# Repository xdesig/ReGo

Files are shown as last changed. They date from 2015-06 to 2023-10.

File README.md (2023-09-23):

# Rego

> [!NOTE]
> Docu in Galician language

Controlador/programador de rego con varias saidas e entradas de sensado

## [Versión 0V3.][ReGo0v3]
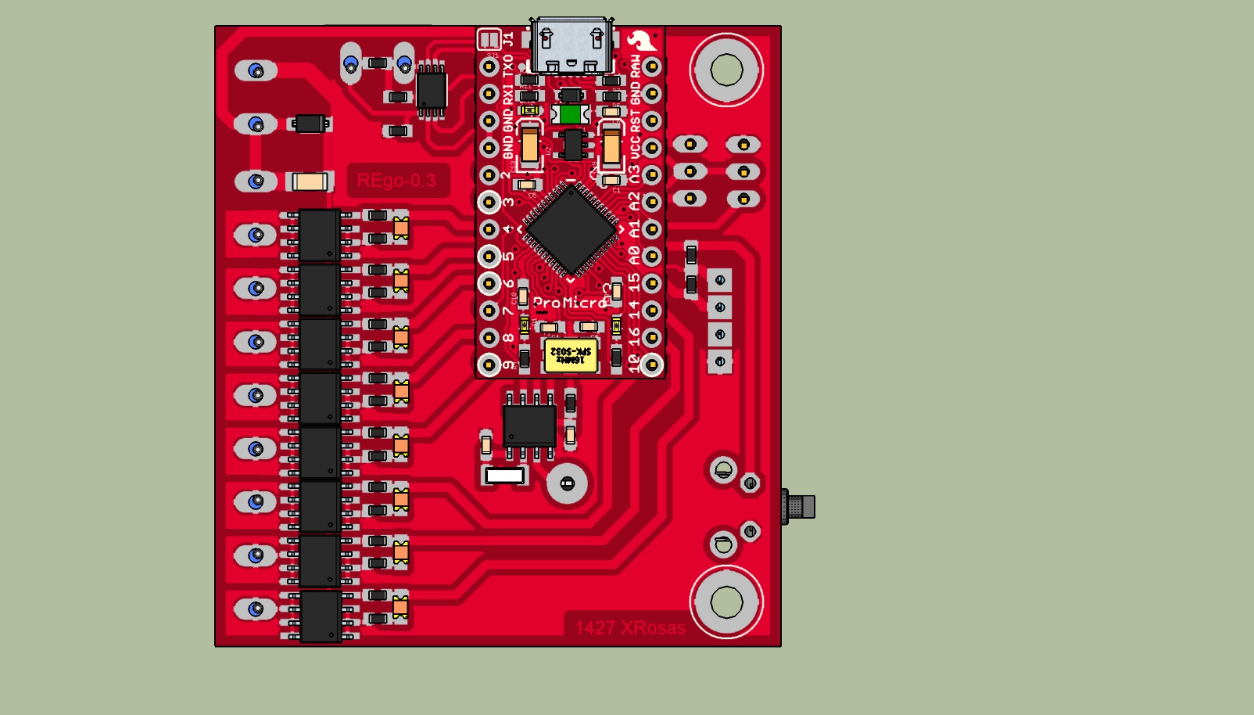
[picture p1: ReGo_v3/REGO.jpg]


Na versión 3 utilizase un Arduino ProMicro, Ten dúas entradas para sensores de humidade, un DTH11 para sensar a humidade e temperatura ambiental permite controlar oito saídas mediante Mosfets en surtidor común. Conta con un RTC PCF8523T e comunicacións USB e I2C

## [Versión 0V401.][ReGo0v4]
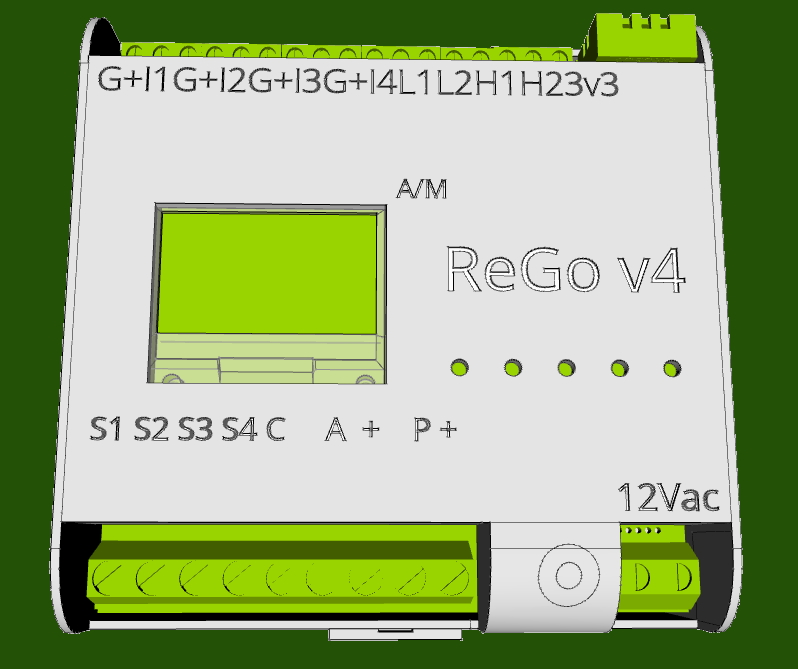
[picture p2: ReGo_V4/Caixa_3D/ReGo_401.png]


Aqui xa temos un ESP-WROOM-32, con comunicación WiFi, ten unha pantalla oled 128x64 pix, unha botoeira analóxica de cinco pulsadores, catro entradas para sensores capacitivos, dúas entradas activas a nivel alto e dúas entradas activas a nivel baixo, que poden ser usadas como finais de carreira para fiestras... ou para outos fins, conta con entrada para sensores tipo DHT11
ten un RTC PCF8523T, catro saídas a SSR (Mosfet) de 1A/30V ac ou DC adicadas xeralmente a activar as electrovalvulas ten tamén dúas saídas en surtidor común 2A/30V (por exemplo para controlar os motoes das fiestras).

* ###  Deseñado en Estrimia con agarimo.

## Author and license
* Author: [XDeSIG][TWI01]
* License: [CERN Open Hardware Licence Version 2 - Weakly Reciprocal][CERN-OHL-W]


* Certification: [OSHWA UID ES000038][OSHWA]

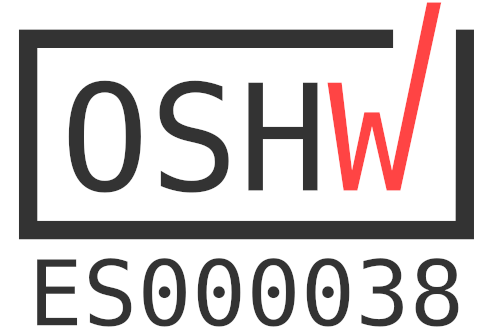
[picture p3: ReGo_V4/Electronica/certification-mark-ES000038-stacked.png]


* ### To buy boards

Developer don't produce boards to sell. Under [_provider_][provider]
directory there are instructions to order yourself.

<!-- links -->
[ReGo0v3]: https://github.com/xdesig/ReGo/tree/master/ReGo_v3
[ReGo0v4]: https://github.com/xdesig/ReGo/tree/master/ReGo_V4

[CERN-OHL-W]: https://ohwr.org/cern_ohl_w_v2.pdf
[TWI01]: https://twitter.com/xdesig
[provider]: https://www.pcbway.com/project/shareproject/Controlador_de_ReGo_V401_bd0da5d6.html
[OSHWA]: https://certification.oshwa.org/es000038.html

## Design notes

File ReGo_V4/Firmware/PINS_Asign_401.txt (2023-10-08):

/*
 * Configuracion de entadas saidas para ReGo 0.401
 * xdesig 2023
 */
// I2C 
#define SDA 
#define SCL 

//*** Entradas ***
// sensores humidade
#define IN_1 39 //SVN  	//Entrada sensor 
#define IN_2 35      	//Entrada sensor 
#define IN_3 33        	//Entrada sensor
#define IN_4 34      	//Entrada sensor

#define KEY 36 //A0     //SPV Entrada teclado 

// finais de carrera
#define IL_1 18      //Entrada Activo baixo 1
#define IL_2 19      //Entrada Activo baixo 2
#define IH_1 23      //Entrada Activo alto 1
#define IH_2 14      //Entrada Activo alto 2 

//*** Salidas ***
// DTH
#define DTHpin 17        //Entrada sensor humidade temperatura DTH

// RTC PCF8523 soldado PCF8563!
#define INT 4         //Interrupción RTC

// Electrovalvúlas
#define SAL_1 27         // Electrovalvúla  
#define SAL_2 25         // Electrovalvúla
#define SAL_3 12  //TD1  // Electrovalvúla 
#define SAL_4  0         // Electrovalvúla 

// Motores
#define ACT_1 2       	 // Pechar
#define ACT_2 15 //TD02  // Abrir

// LED Auto/Manual
#define GREEN 9       // GREEN (RED = 0 GREEN = 1) SD3
#define RED 10        // RED   (RED = 1 GREEN = 0) SD2

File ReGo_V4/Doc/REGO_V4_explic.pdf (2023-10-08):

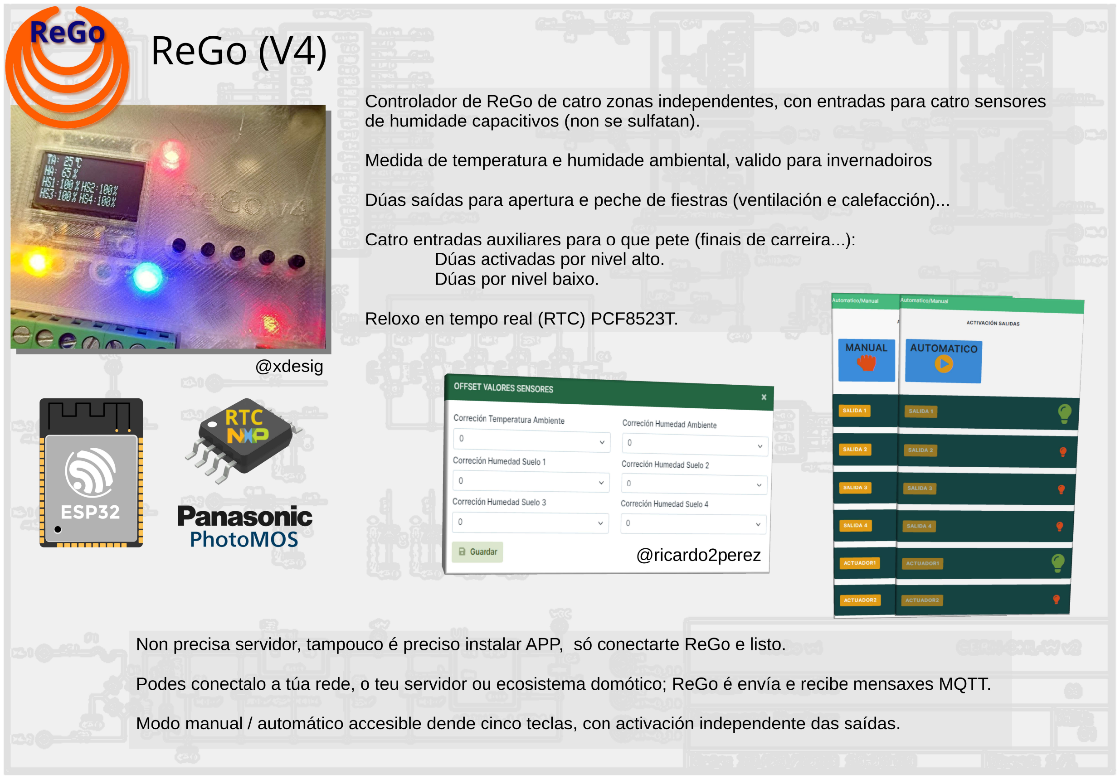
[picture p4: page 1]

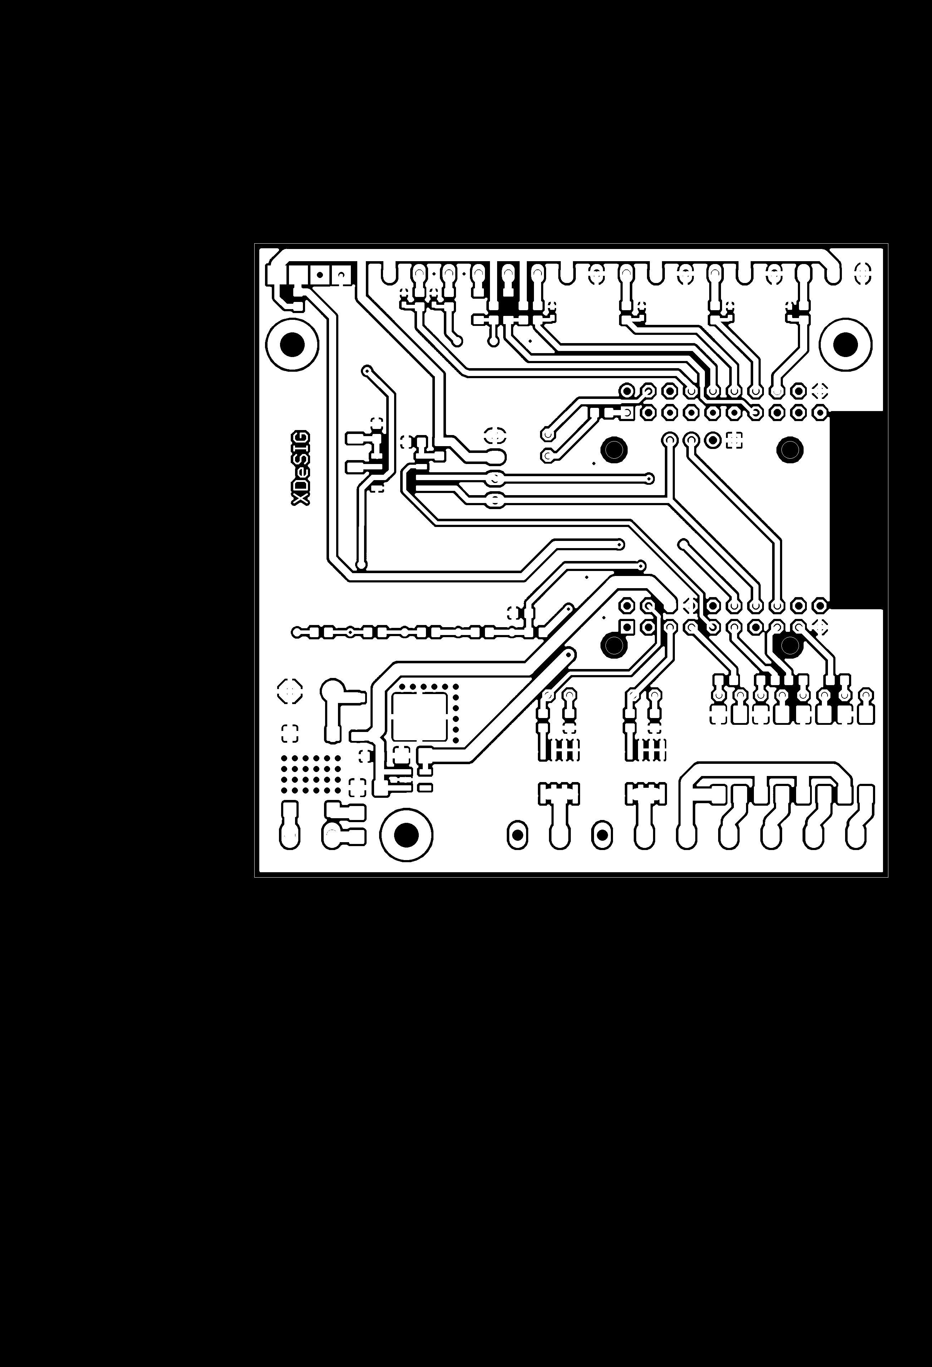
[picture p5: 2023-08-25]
ReGo_V4/Electronica/ReGo_V401_cu_Top.png

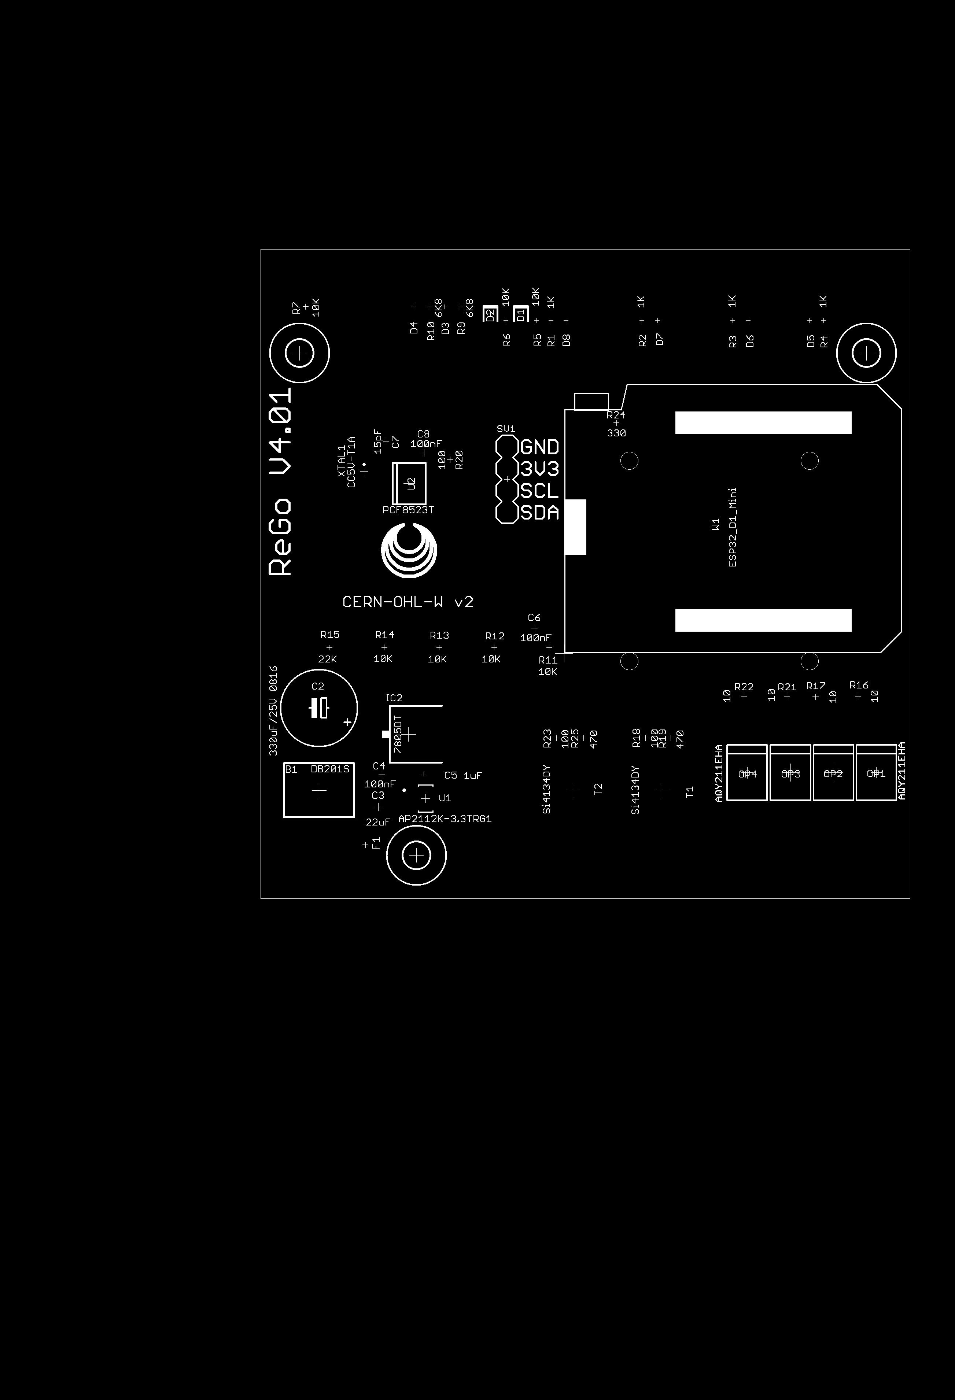
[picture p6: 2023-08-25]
ReGo_V4/Electronica/ReGo_V401_Doc_Top.png

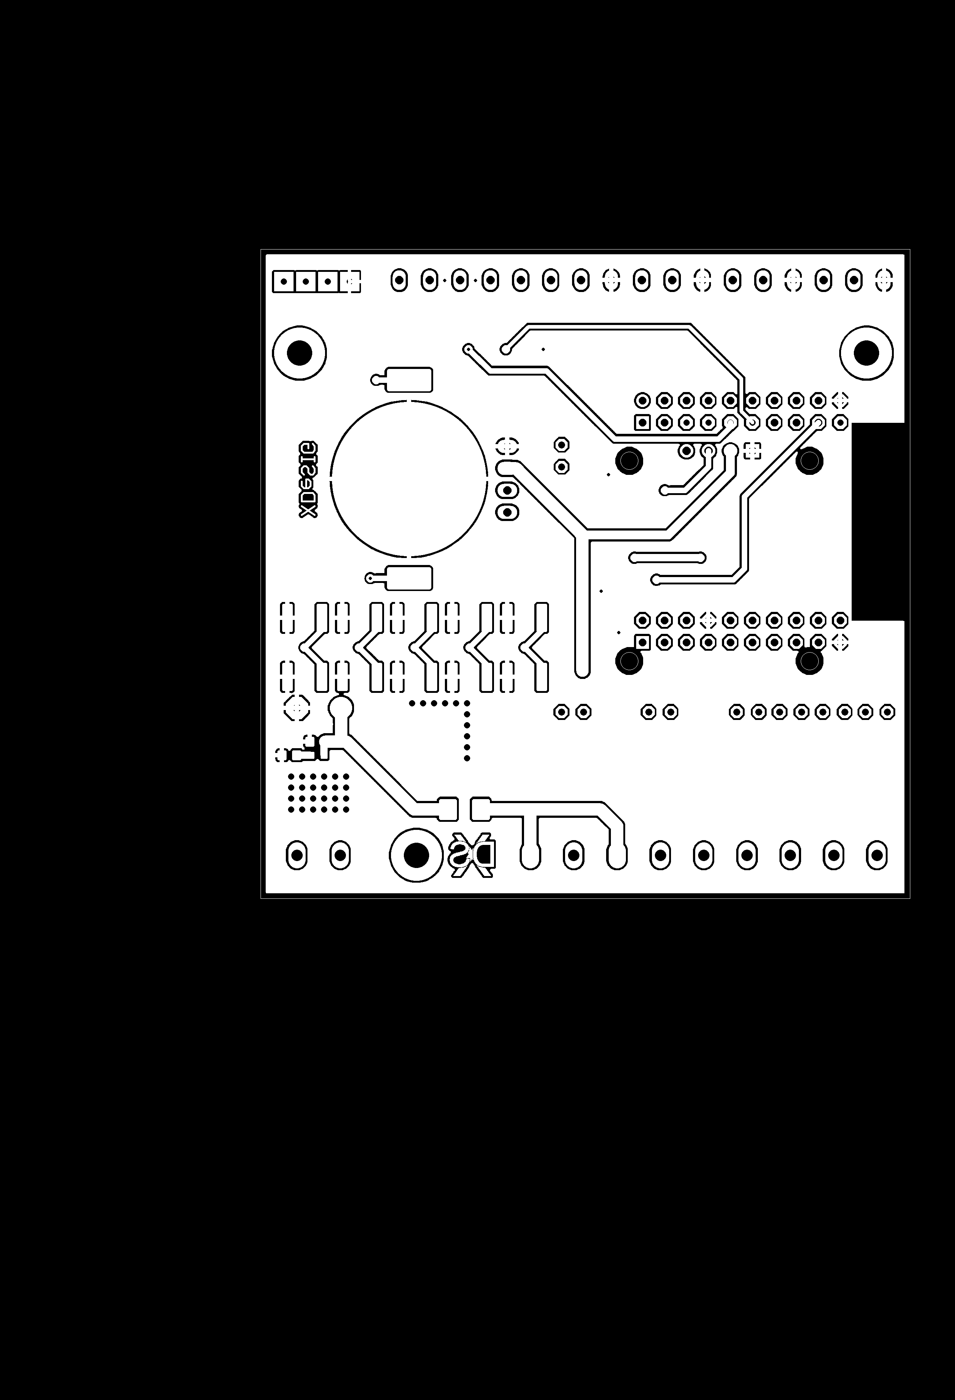
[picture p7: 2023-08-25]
ReGo_V4/Electronica/ReGo_V401_cu_Bot.png

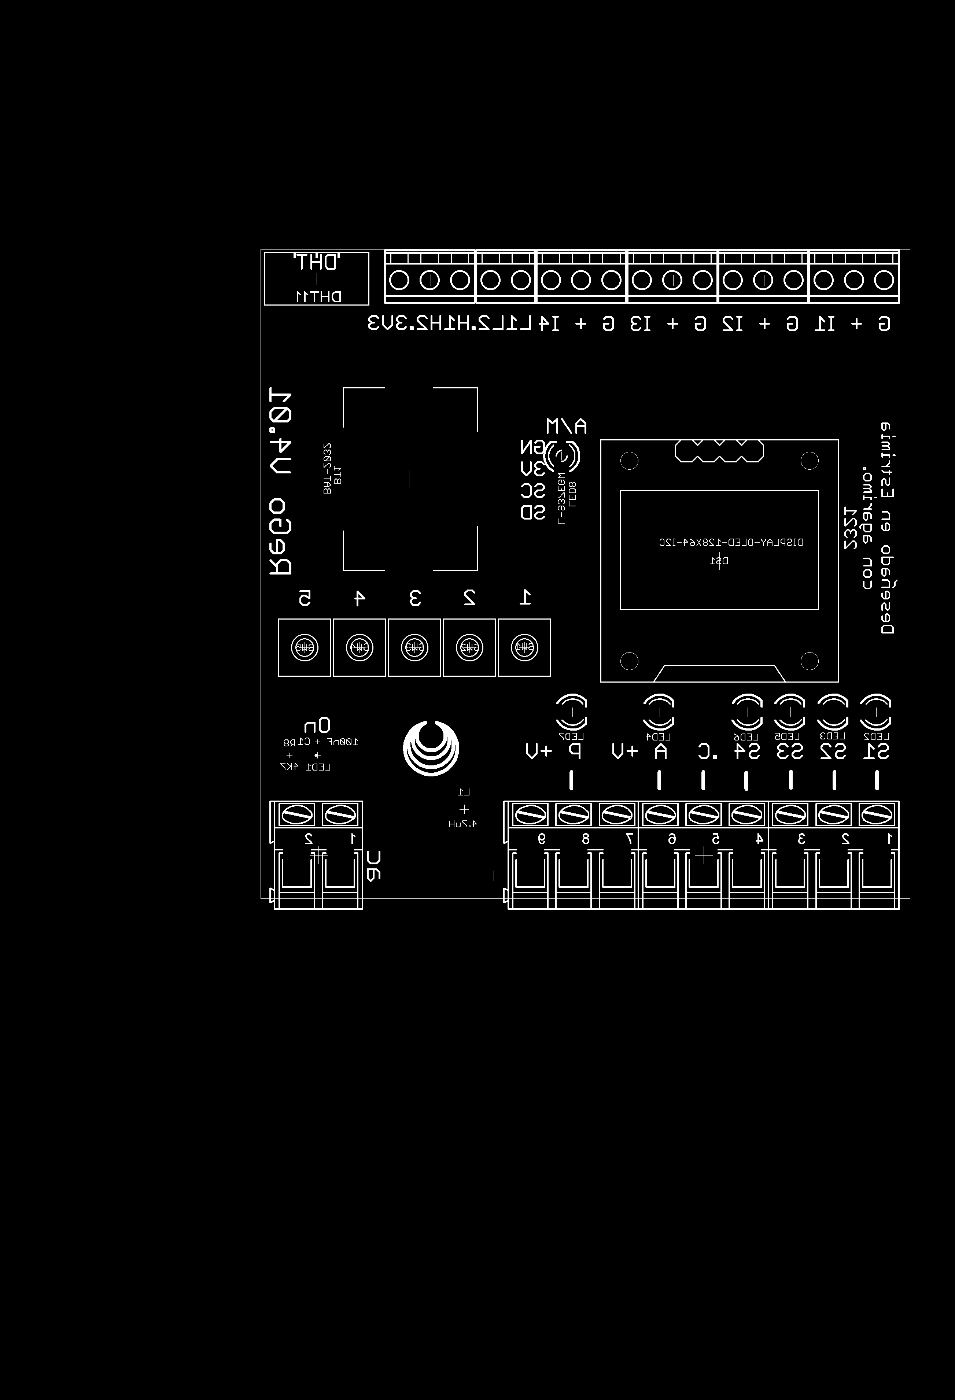
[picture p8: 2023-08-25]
ReGo_V4/Electronica/ReGo_V401_Doc_Bot.png

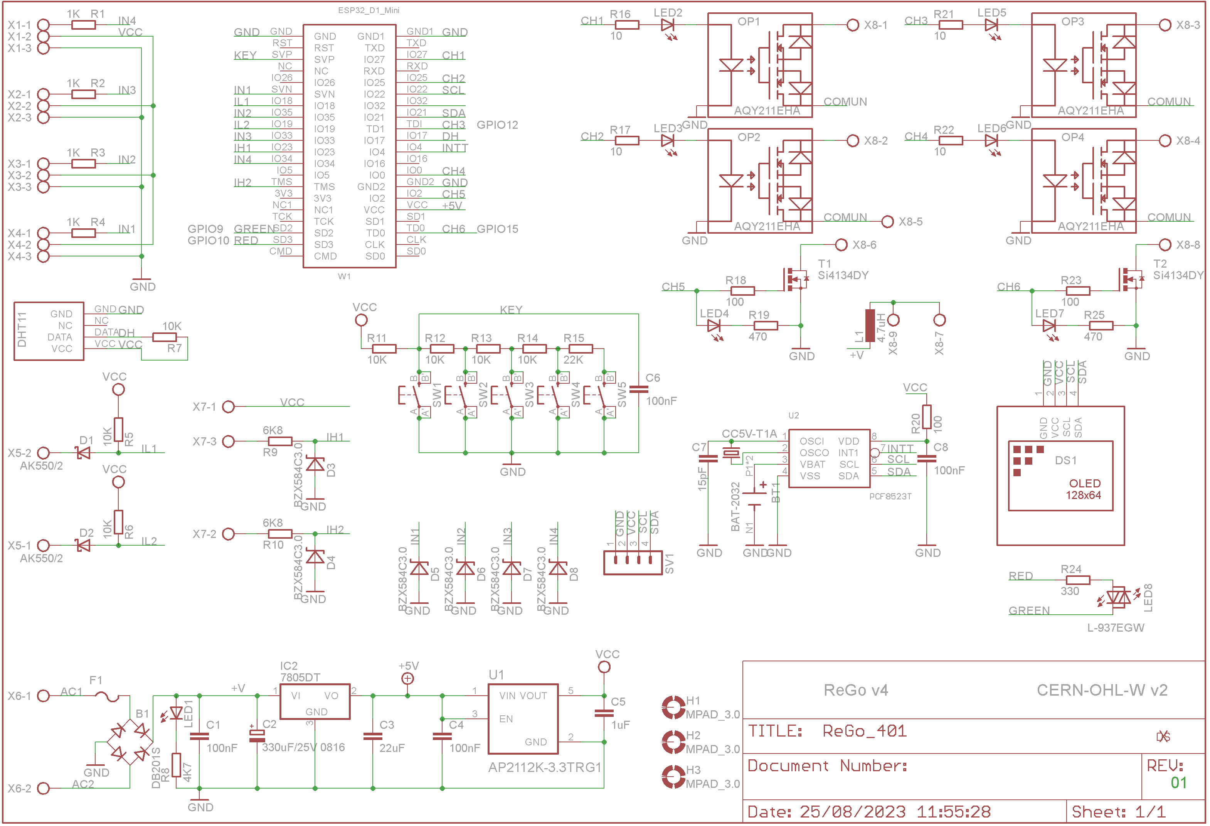
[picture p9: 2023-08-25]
ReGo_V4/Electronica/ReGo_V401_ESQ.png

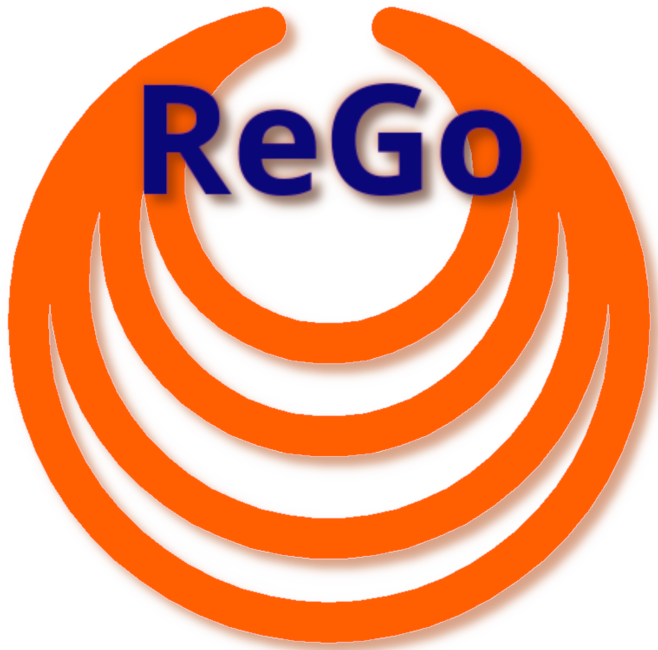
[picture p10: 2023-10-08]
ReGo_V4/Doc/ReGo_V401_Logo.png

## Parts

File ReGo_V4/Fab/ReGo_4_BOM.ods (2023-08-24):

Qty | Value | Device | Package | Parts | Description | SUPPLIER
1 |  | AK300/2 | AK300/2 | X6
1 |  | AK300/9 | AK300/9 | X8
5 |  | AK550/3 | AK550/3 | X1, X2, X3, X4, X7
2 |  | DIODE_SCHOTTKYSOD123FL | DIODE_SOD123FL | D1, D2
6 |  | LED3MM | LED3MM | LED2, LED3, LED4, LED5, LED6, LED7
1 |  | LEDCHIPLED_0603 | CHIPLED_0603 | LED1
1 |  | MA04-1 | MA04-1 | SV1
1 |  | PTCFUSE-1206 | R1206 | F1
2 |  | R-EU_R0603 | R0603 | R8, R23
4 | 10R | R-EU_R0603 | R0603 | R16, R17, R21, R22
3 | 100R | R-EU_R0603 | R0603 | R18, R20, R24
5 | 100nF | C-EUC0603K | C0603K | C1, C5, C6, C7, C9
7 | 10K | R-EU_R0603 | R0603 | R5, R6, R7, R11, R12, R13, R14
1 | 15pF | C-EUC0603 | C0603 | C8
4 | 1K | R-EU_R0603 | R0603 | R1, R2, R3, R4
1 | 22K | R-EU_R0603 | R0603 | R15
3 | 22uF | C-EUC1206 | C1206 | C2, C3, C4
2 | 470R | R-EU_R0603 | R0603 | R19, R25
2 | 6K8 | R-EU_R0603 | R0603 | R9, R10
1 | 7805DT | 7805DT | TO252 | IC2
1 | AK550/2 | AK550/2 | AK550/2 | X5
4 | AQY211EHA | AQY211EHA | DIL4-SMD | OP1, OP2, OP3, OP4
5 | B3U-1000P | 0173_IT-1185AP1C-160G-G_T&R | SMD_157SW | S1, S2, S3, S4, S5 |  | _____
1 | BAT-HLD-001 | BAT-HLD-001 | BAT_BAT-HLD-001 | BT1
6 | BZX584C3.0 | BZX584C | SOD523 | D3, D4, D5, D6, D7, D8
1 | CC5V-T1A | CC5V-T1A | T1A | U$1
1 | DB201S | RECTIFIER-B40S | B40S | B1
1 | DHT11-PION. | DHT11-PION. | DHT11-PION. | IC1
1 | DISPLAY-OLED-128X64-I2C | DISPLAY-OLED-128X64-I2C | DISPLAY-OLED-128X64-I2C | DS1
1 | ESP32_D1_Mini | WEMOS_MINI_ESP32 | WEMOS_MINI_32 | W1
1 | J5MM | J5MM | 5 | J1
1 | L-937EGW | LED_BI_3MM | LED_LED3MM | LED8
1 | LD117AS33TR | LD117AS33TR | SOT223 | IC3
3 | MPAD_3.0 | MOUNT-PAD-ROUND3.0 | 3,0-PAD | H1, H2, H3
1 | PCF8523T | PCF8523T | SOT96-1 | U1
2 | Si4134DY | SI4134DY | SO-08 | T1, T2

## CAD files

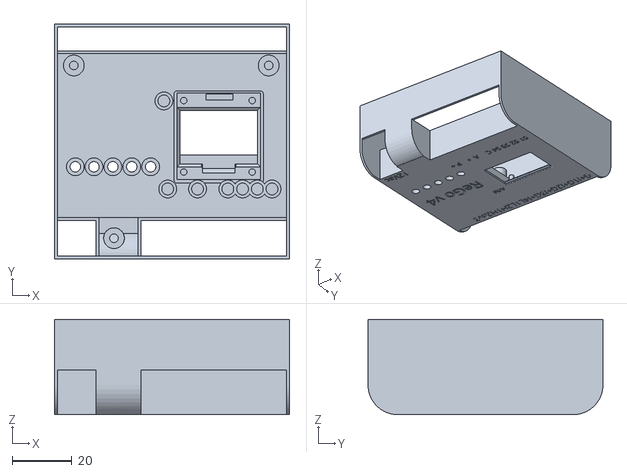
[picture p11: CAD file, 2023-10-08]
ReGo_V4/Caixa_3D/ReGo_401_caixa_Dianteira.stl
79.0 x 79.0 x 32.0

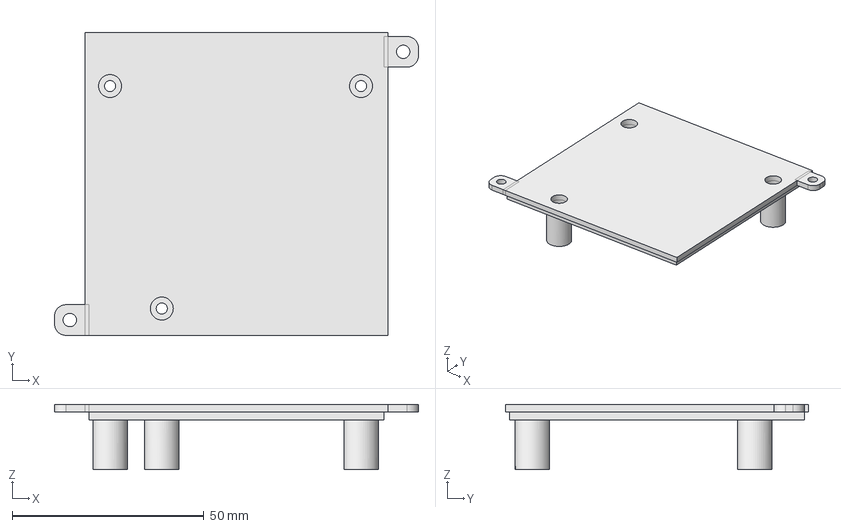
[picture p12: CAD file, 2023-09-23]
ReGo_V4/Caixa_3D/ReGo_401_caixa_traseira.step
95.0 x 79.0 x 17.0 mm

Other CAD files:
ReGo_V4/Caixa_3D/ReGo_401_caixa_Traseira.stl

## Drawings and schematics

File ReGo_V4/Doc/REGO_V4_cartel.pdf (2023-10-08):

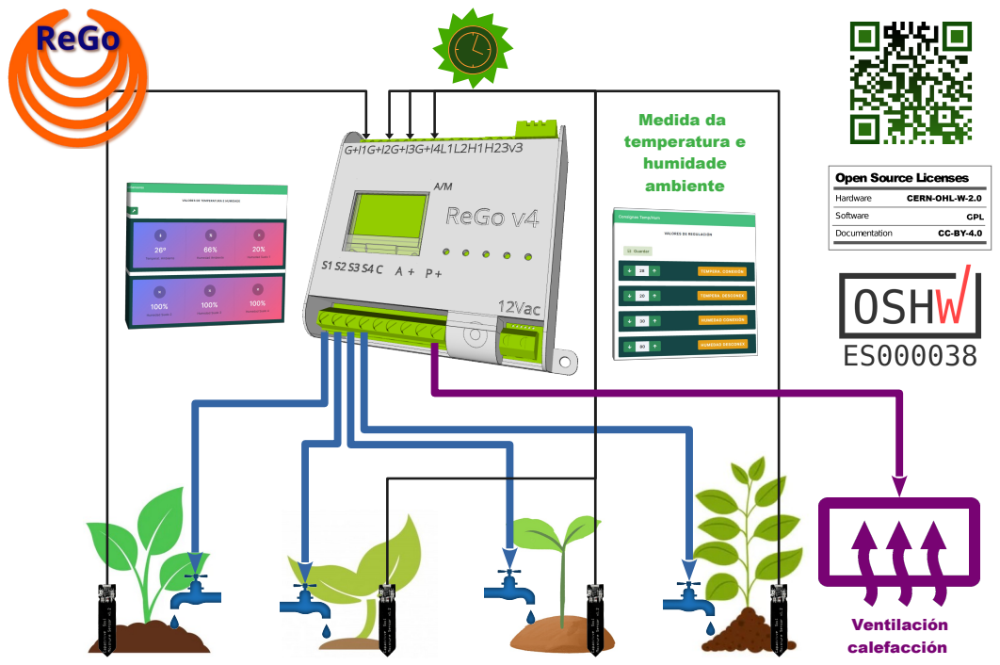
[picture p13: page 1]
Ventilación calefacción; Medida da temperatura e humidade ambiente

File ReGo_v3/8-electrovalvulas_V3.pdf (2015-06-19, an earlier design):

E1

E2

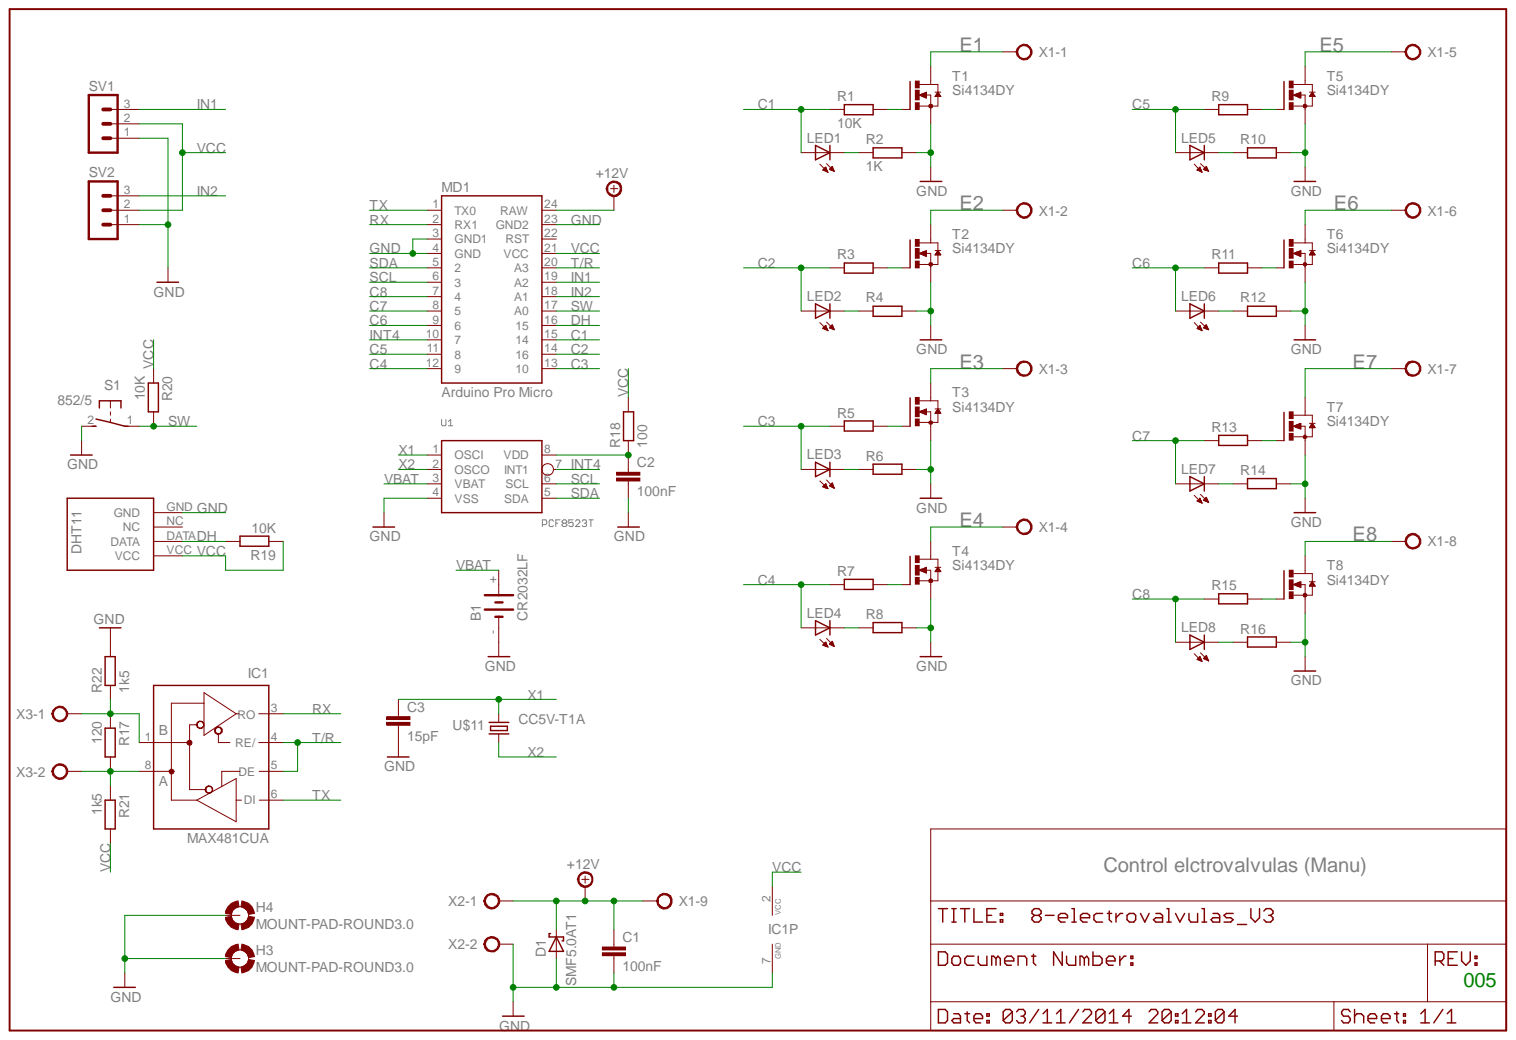
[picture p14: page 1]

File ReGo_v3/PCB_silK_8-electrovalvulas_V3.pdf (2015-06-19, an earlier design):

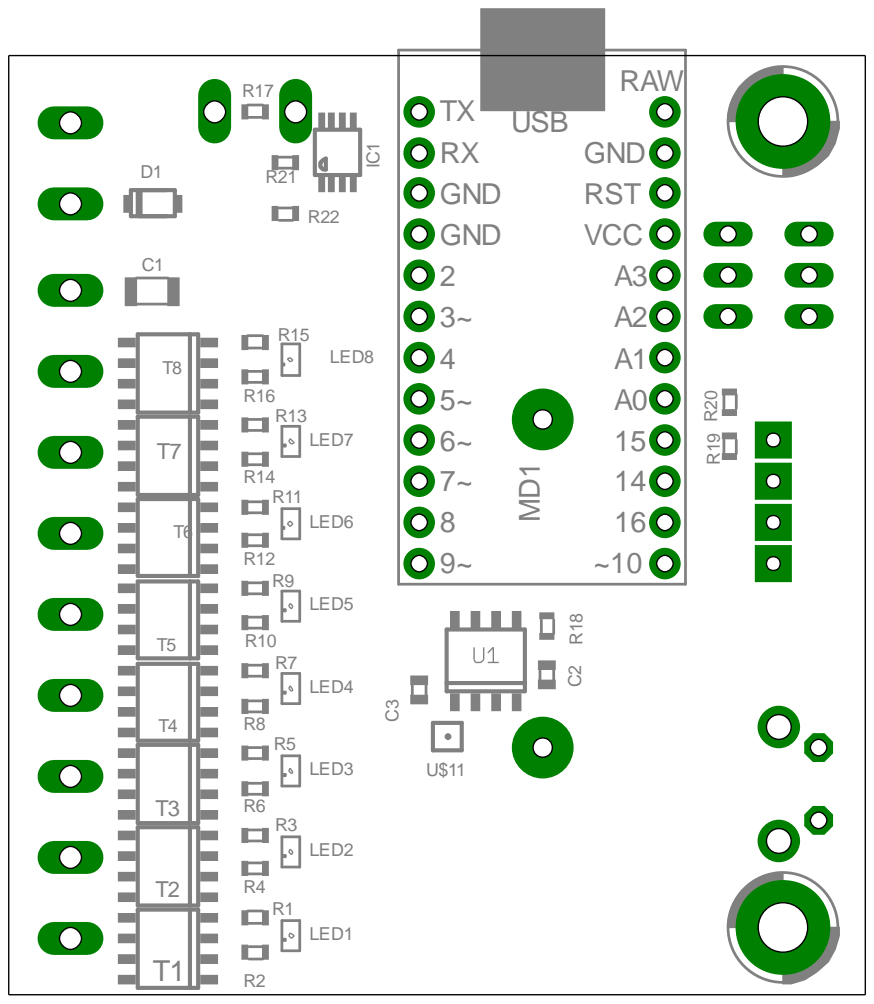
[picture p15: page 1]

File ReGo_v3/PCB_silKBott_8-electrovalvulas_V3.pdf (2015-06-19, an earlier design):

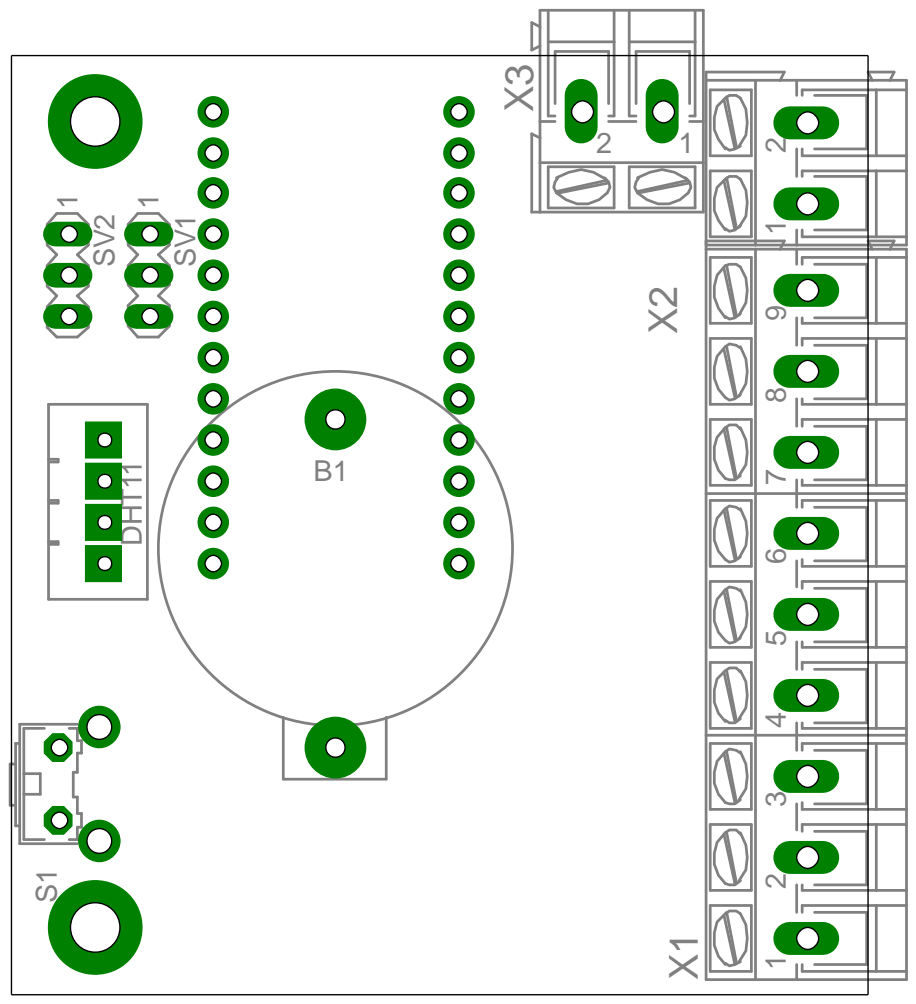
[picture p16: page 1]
DHT11

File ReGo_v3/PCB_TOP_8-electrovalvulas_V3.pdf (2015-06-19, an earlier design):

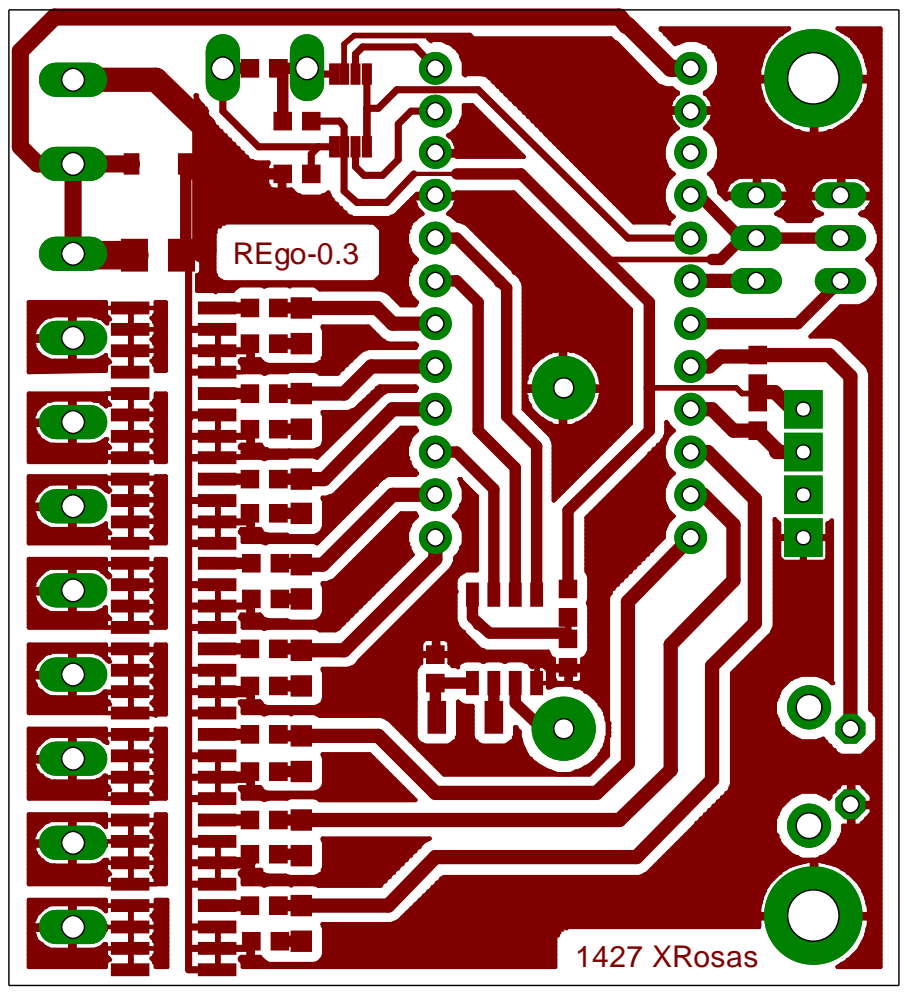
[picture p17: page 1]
REgo-0.3; 1427 XRosas

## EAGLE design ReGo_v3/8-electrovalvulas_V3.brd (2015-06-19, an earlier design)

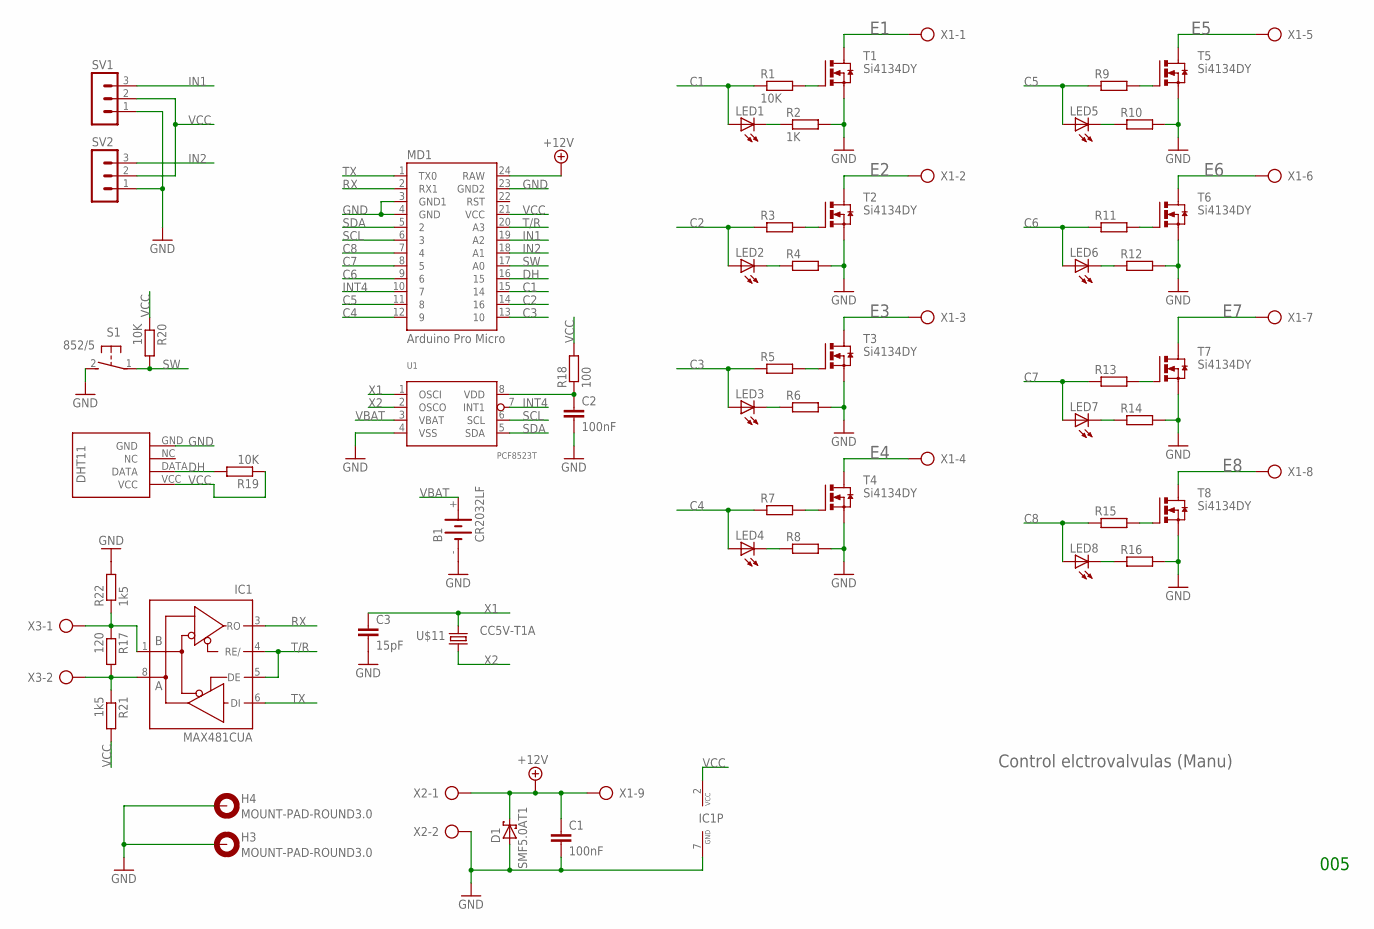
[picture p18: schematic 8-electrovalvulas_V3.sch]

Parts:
B1: CR2032LF; BATTERY_1236_C
C1: 100nF; C1206
C2: 100nF; C0603
C3: 15pF; C0603
D1: SMF5.0AT1; SOD123FL
H3, H4: MOUNT-PAD-ROUND3.0; 3,0-PAD
IC1: MAX481CUA; UMAX8
IC10: DHT11-PION.
LED1, LED2, LED3, LED4, LED5, LED6, LED7, LED8: LEDSML0805; SML0805
MD1: Arduino Pro Micro; PRO_MICRO
R1, R19, R20: 10K; R0603
R2: 1K; R0603
R3, R4, R5, R6, R7, R8, R9, R10, R11, R12, R13, R14, R15, R16: R-EU_R0603; R0603
R17: 120; R0603
R18: 100; R0603
R21, R22: 1k5; R0603
S1: 852/5; B3F-31XX
SV1, SV2: MA03-1
T1, T2, T3, T4, T5, T6, T7, T8: Si4134DY; SO-08
U1: PCF8523T; SOT96-1
U$11: CC5V-T1A; T1A
X1: AK300/9
X2, X3: AK300/2

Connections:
+12V: C1.1, D1.C, MD1.24 (RAW), X1.9, X2.1
A: IC1.8 (A), R17.2, R21.1, X3.2
B: IC1.1 (B), R17.1, R22.1, X3.1
C1: LED1.A, MD1.15 (14), R1.1
C2: LED2.A, MD1.14 (16), R3.1
C3: LED3.A, MD1.13 (10), R5.1
C4: LED4.A, MD1.12 (9), R7.1
C5: LED5.A, MD1.11 (8), R9.1
C6: LED6.A, MD1.9 (6), R11.1
C7: LED7.A, MD1.8 (5), R13.1
C8: LED8.A, MD1.7 (4), R15.1
DH: IC10.DATA, MD1.16 (15), R19.2
E1: T1.5 (D), T1.6 (D), T1.7 (D), T1.8 (D), X1.1
E2: T2.5 (D), T2.6 (D), T2.7 (D), T2.8 (D), X1.2
E3: T3.5 (D), T3.6 (D), T3.7 (D), T3.8 (D), X1.3
E4: T4.5 (D), T4.6 (D), T4.7 (D), T4.8 (D), X1.4
E5: T5.5 (D), T5.6 (D), T5.7 (D), T5.8 (D), X1.5
E6: T6.5 (D), T6.6 (D), T6.7 (D), T6.8 (D), X1.6
E7: T7.5 (D), T7.6 (D), T7.7 (D), T7.8 (D), X1.7
E8: T8.5 (D), T8.6 (D), T8.7 (D), T8.8 (D), X1.8
GND: B1.-, C1.2, C2.2, C3.2, D1.A, H3.B3,0, H4.B3,0, IC1.7 (GND), IC10.GND, MD1.3 (GND1), MD1.4 (GND), MD1.23 (GND2), R2.2, R4.2, R6.2, R8.2, R10.2, R12.2, R14.2, R16.2, R22.2, S1.2 (S), SV1.1, SV2.1, T1.1 (S), T1.2 (S), T1.3 (S), T2.1 (S), T2.2 (S), T2.3 (S), T3.1 (S), T3.2 (S), T3.3 (S), T4.1 (S), T4.2 (S), T4.3 (S), T5.1 (S), T5.2 (S), T5.3 (S), T6.1 (S), T6.2 (S), T6.3 (S), T7.1 (S), T7.2 (S), T7.3 (S), T8.1 (S), T8.2 (S), T8.3 (S), U1.4 (VSS), X2.2
IN1: MD1.19 (A2), SV1.3
IN2: MD1.18 (A1), SV2.3
INT4: MD1.10 (7), U1.7 (INT1)
unnamed: R1.2, T1.4 (G)
unnamed: LED1.C, R2.1
unnamed: R3.2, T2.4 (G)
unnamed: C2.1, R18.1, U1.8 (VDD)
unnamed: LED2.C, R4.1
unnamed: R5.2, T3.4 (G)
unnamed: LED3.C, R6.1
unnamed: R7.2, T4.4 (G)
unnamed: R9.2, T5.4 (G)
unnamed: LED4.C, R8.1
unnamed: LED5.C, R10.1
unnamed: R11.2, T6.4 (G)
unnamed: LED6.C, R12.1
unnamed: R13.2, T7.4 (G)
unnamed: LED7.C, R14.1
unnamed: R15.2, T8.4 (G)
unnamed: LED8.C, R16.1
RX: IC1.3 (RO), MD1.2 (RX1)
SCL: MD1.6 (3), U1.6 (SCL)
SDA: MD1.5 (2), U1.5 (SDA)
SW: MD1.17 (A0), R20.2, S1.1
T/R: IC1.4 (RE/), IC1.5 (DE), MD1.20 (A3)
TX: IC1.6 (DI), MD1.1 (TX0)
VBAT: B1.+, U1.3 (VBAT)
VCC: IC1.2 (VCC), IC10.VCC, MD1.21 (VCC), R18.2, R19.1, R20.1, R21.2, SV1.2, SV2.2
X1: C3.1, U1.1 (OSCI), U$11.2
X2: U1.2 (OSCO), U$11.1

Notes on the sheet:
Control elctrovalvulas (Manu)
005

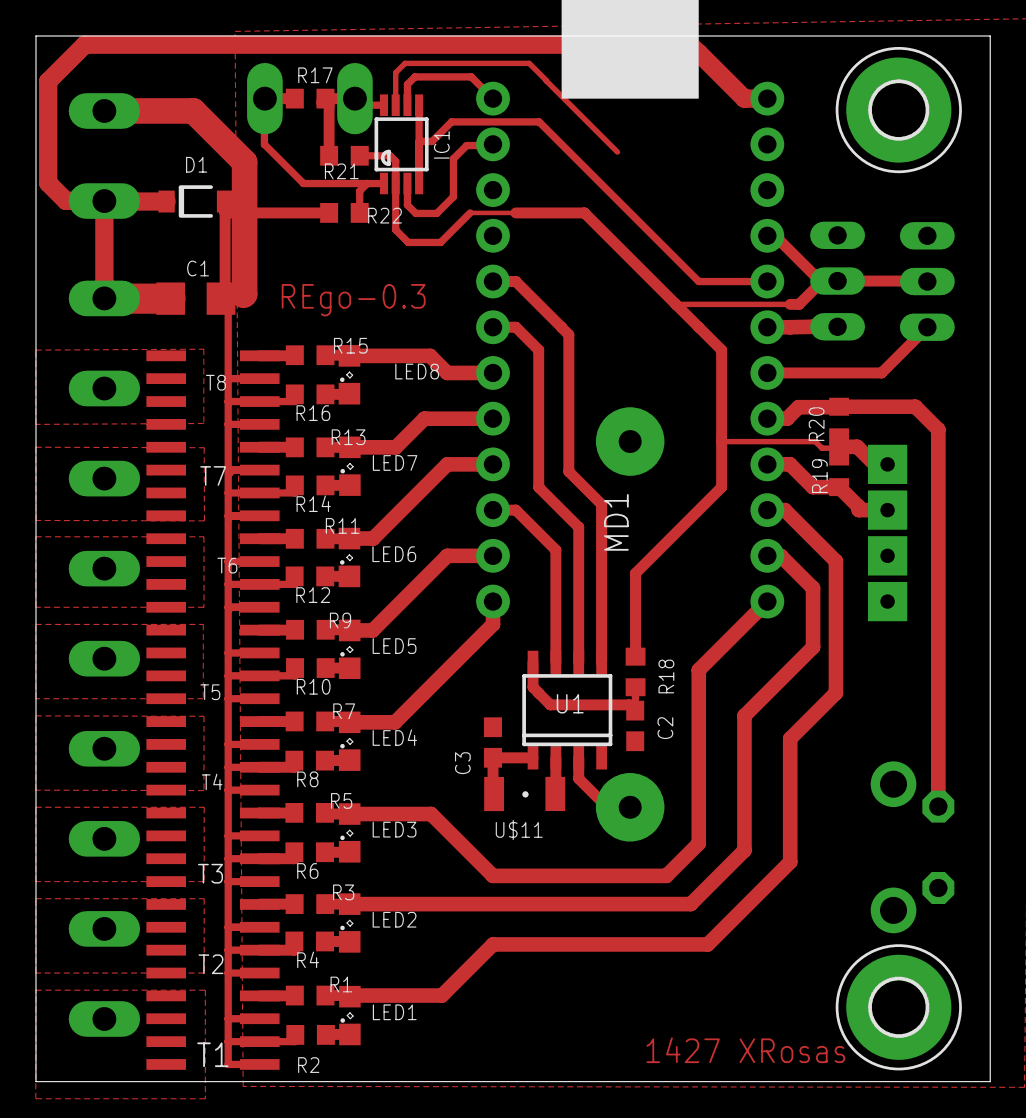
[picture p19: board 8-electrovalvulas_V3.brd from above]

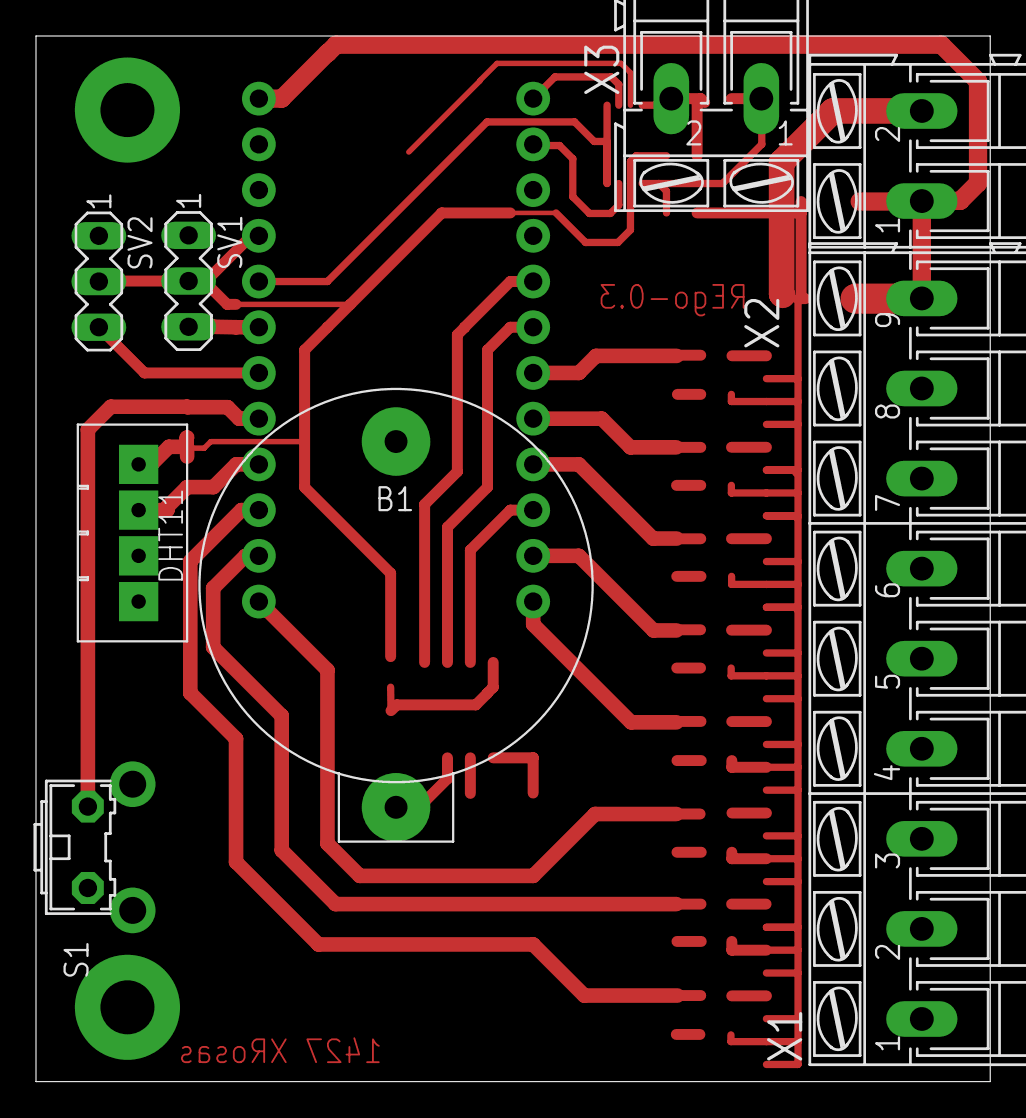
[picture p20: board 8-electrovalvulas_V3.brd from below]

Board: 2 copper layers, 53.0 x 58.1 mm, 56 parts (8 on the bottom side), 51 nets.

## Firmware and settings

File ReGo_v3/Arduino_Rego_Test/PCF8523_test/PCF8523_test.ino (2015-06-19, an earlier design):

/*  *************************
    FILE: ReGo_Test
    X Rosas.
  Test placa ReGo 0.3
  *************************

 Transmite o mesmo por USB e RS485 ( menos o time que só por USB)

 SDA 2
 SCL 3
 interrupción RTC INT4
 Tx 0
 Rx 1
 tranmisión / recepcion A3
*/

/*          PCF8523 Arduino library
    Copyright (C) Alfredo Prado ,2014
    radikalbytes [at] gmail [dot] com


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
  The author disclaim all warranties with regard to this
  software, including all implied warranties of merchantability
  and fitness.  In no event shall the author be liable for any
  special, indirect or consequential damages or any damages
  whatsoever resulting from loss of use, data or profits, whether
  in an action of contract, negligence or other tortious action,
  arising out of or in connection with the use or performance of
  this software.
*/

#include "Wire.h"

#include <PCF8523.h>
PCF8523 rtc;
int segundos = 0;

int C_1 = 14;
int C_2 = 16;
int C_3 = 10;
int C_4 = 9;
int C_5 = 8;
int C_6 = 6;
int C_7 = 5;
int C_8 = 4;

  

void setup(){
pinMode(2, INPUT);           // set pin to input
digitalWrite(2, HIGH);       // turn on pullup resistors
pinMode(3, INPUT);           // set pin to input
digitalWrite(3, HIGH);       // turn on pullup resistors

  pinMode(C_1, OUTPUT);
  pinMode(C_2, OUTPUT);
  pinMode(C_3, OUTPUT);
  pinMode(C_4, OUTPUT);
  pinMode(C_5, OUTPUT);
  pinMode(C_6, OUTPUT);
  pinMode(C_7, OUTPUT);
  pinMode(C_8, OUTPUT);  


  Wire.begin();
  Serial.begin(115200);
  Serial.println("Initializing RTC...");
#ifdef AVR
  Wire.begin();
#else
  Wire1.begin(); // Shield I2C pins connect to alt I2C bus on Arduino Due
#endif
  rtc.begin();
  rtc.adjust(DateTime(2014, 11, 16, 15, 25, 0));

  if (! rtc.isrunning()) {
    Serial.println("RTC is NOT running!");
    // following line sets the RTC to the date & time this sketch was compiled
   //rtc.adjust(DateTime(F(__DATE__), F(__TIME__)));
    // This line sets the RTC with an explicit date & time, for example to set

  
  }
 
 }

void loop(){
    DateTime now = rtc.now();
    
    Serial.print(now.year(), DEC);
    Serial.print('/');
    Serial.print(now.month(), DEC);
    Serial.print('/');
    Serial.print(now.day(), DEC);
    Serial.print(' ');
    Serial.print(now.hour(), DEC);
    Serial.print(':');
    Serial.print(now.minute(), DEC);
    Serial.print(':');
    Serial.print(now.second(), DEC);
    Serial.println();
    

    // Canles de Saida
  digitalWrite(C_1, HIGH);   
  delay(100);                
  digitalWrite(C_1, LOW); 
  digitalWrite(C_2, HIGH);   
  delay(100);                
  digitalWrite(C_2, LOW); 
  digitalWrite(C_3, HIGH);   
  delay(100);                
  digitalWrite(C_3, LOW); 
  digitalWrite(C_4, HIGH);   
  delay(100);                
  digitalWrite(C_4, LOW); 
  digitalWrite(C_5, HIGH);   
  delay(100);                
  digitalWrite(C_5, LOW); 
  digitalWrite(C_6, HIGH);   
  delay(100);                
  digitalWrite(C_6, LOW); 
  digitalWrite(C_7, HIGH);   
  delay(100);                
  digitalWrite(C_7, LOW); 
  digitalWrite(C_8, HIGH);   
  delay(100);                
  digitalWrite(C_8, LOW); 

}
